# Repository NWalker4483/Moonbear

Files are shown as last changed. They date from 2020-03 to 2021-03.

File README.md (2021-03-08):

<div align="center">

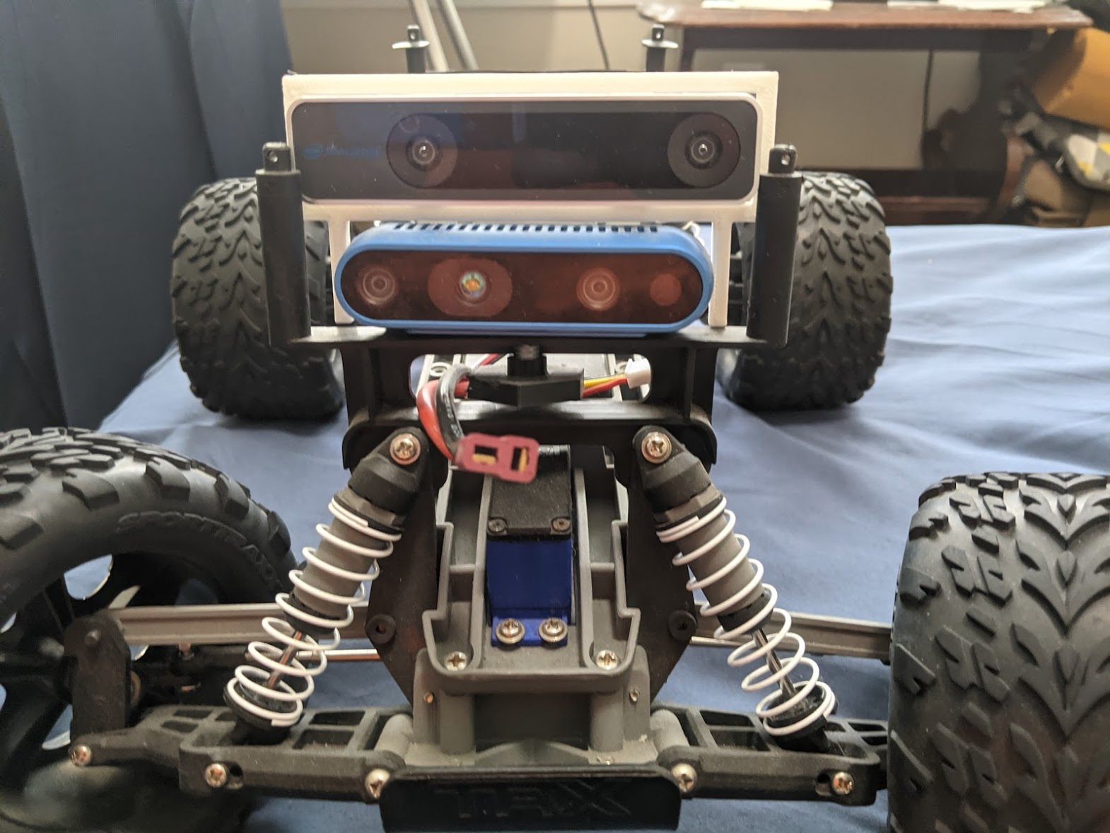
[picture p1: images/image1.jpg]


# Morgan State University’s School of Engineering
## MSU RACECAR V1





# Table of contents
</div>

1. [Introduction](#intro)
2. [The Build Construction](#paragraph1)
   1. Bill of Materials
   2. Compute Modules
   3. Camera(s)
   4. Wi-Fi
   5. Assembly Hardware
3. Hardware Setup
   1. 3D Printed Parts
   2. Wiring
4. The Software Setup
   1. ROS
   2. Arduino
   3. Bluetooth
5. Startup
   1. Manual
   2. Autonomous

## Introduction 
Morgan State University is attempting to delve into the world of Artificial Intelligence. This project is meant to act as a jumping off point for a future endeavors and build a platform that students can learn from and build upon.



## The Build Construction 

### Bill of Materials 

This section lists the parts needed to build the MSU RACECAR. After you have received the parts and confirmed them, proceed to the hardware setup. Some of the parts are 3D printed. In these cases, the STL files have been made available along with recommended print settings.

```Disclaimer: Most of the URLs are from the OEM. You can probably find it cheaper elsewhere, e.g. Amazon.```

### Computing Modules (?) 
|                        |          |        |                                                                                                                                                                                                                                                                                                                |                                |
| ---------------------- | -------- | ------ | -------------------------------------------------------------------------------------------------------------------------------------------------------------------------------------------------------------------------------------------------------------------------------------------------------------- | ------------------------------ |
| Part                   | Quantity | Cost   | URL                                                                                                                                                                                                                                                                                                            | Note                           |
| Jetson Nano            | 1        | $99.00 | https://www.nvidia.com/en-us/autonomous-machines/jetson-store/#jetson-Nano                                                                                                                                                                                                                                     | The 2GB version is also        |
| Arduino Micro          | 1        | $32.00 | https://store.arduino.cc/usa/arduino-micro                                                                                                                                                                                                                                                                     | Generic Version will work also |
### Camera(s) 
|            |          |         |                                                                                                                                                                                                                                                                                                                                                                                                           |      |
| ---------- | -------- | ------- | --------------------------------------------------------------------------------------------------------------------------------------------------------------------------------------------------------------------------------------------------------------------------------------------------------------------------------------------------------------------------------------------------------- | ---- |
| Part       | Quantity | Cost    | URL                                                                                                                                                                                                                                                                                                                                                                                                       | Note |
| INTEL D435 | 1        | $179.00 | https://store.intelrealsense.com/buy-intel-realsense-depth-camera-d435.html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    |      |
| INTEL T265 | 1        | $199.00 | https://store.intelrealsense.com/buy-intel-realsense-tracking-camera-t265.html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 |      |

### Wi-Fi 
|           |          |        |                                                                                                                                                                                                                                                                                                                                                                                                                                                                                              |      |
| --------- | -------- | ------ | -------------------------------------------------------------------------------------------------------------------------------------------------------------------------------------------------------------------------------------------------------------------------------------------------------------------------------------------------------------------------------------------------------------------------------------------------------------------------------------------- | ---- |
| Part      | Quantity | Cost   | URL                                                                                                                                                                                                                                                                                                                                                                                                                                                                                          | Note |
| TL-WN722N | 1        | $16.99 | https://www.tp-link.com/us/home-networking/usb-adapter/tl-wn722n/                                                                                                                                                                                                                                                                                                                                                                                                                            |      |
| USB Hub   | 1        | $12.99 | https://www.amazon.com/Anker-Extended-MacBook-Surface-Notebook/dp/B07L32B9C2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 |      |
### Assembly Hardware + Misc 
|                                              |          |       |                                                                               |                                                                                    |
| -------------------------------------------- | -------- | ----- | ----------------------------------------------------------------------------- | ---------------------------------------------------------------------------------- |
| Part                                         | Quantity | Cost  | URL                                                                           | Note                                                                               |
| Chassis                                      | 1        | $275  |                                                                               | Purchasing a different chassis may make some of the 3-D printed parts unusable     |
| M3 x 6 Machine Screws                        | 4        |       |                                                                               |                                                                                    |
| M5 x 6 Machine Screws                        | 1        |       |                                                                               |                                                                                    |
| 20 x 40 Perfboard                            | 1        | $3    |                                                                               |                                                                                    |
| LM2596 DC-DC Buck Converter Step Down Module | 1        | 14.95 | https://www.amazon.com/LM2596-Converter-Module-Supply-1-23V-30V/dp/B008BHBEE0 | The actual individual part is much cheaper but is often sold only in packs of 5-10 |

## Hardware Setup

### 3D Printed Parts

```All Parts where 3D printed on an Ender 3```
|                                                                                             |                                                                                                                                                                                |                 |              |            |
| ------------------------------------------------------------------------------------------- | ------------------------------------------------------------------------------------------------------------------------------------------------------------------------------ | --------------- | ------------ | ---------- |
| Image(s)                                                                                    | Purpose                                                                                                                                                                        | Supports Needed | Layer Height | Printspeed |
| <img width="200px"  src="images/image3.jpg"/><img width="200px"  src="images/image11.jpg"/> | Acts as a mount for the 2 3D Sensing Cameras. This piece is screwed directly into the front frame of the car as shown in pictures                                              | No              | .28mm        | 150mm/s    |
| <img width="200px"  src="images/image8.jpg"/>                                               | Screws into the rear underside of the Jetson Nano, while the front side rests on a piece of foam on top of the ESC                                                             | Yes             | .28mm        | 150mm/s    |
| <img width="200px"  src="images/image9.jpg"/><img width="200px"  src="images/image10.jpg"/> | Screws into the body of the ESC and attaches to the sides of the arduinos perf board. These pieces are designed specifically for this frame and should slide in place as shown | Yes             | .28mm        | 150mm/s    |
| <img width="200px"  src="images/image12.jpeg"/>                                             | *Take better photo* Acts to extend the head of a 5mm bolt <br>```Before installing drill an approximately 6 mm hole in the middle of the front facing crossbar and shown in the introductory photo```                                                             | No              | .28mm        | 150mm/s    |

### Construction 
#### Power

<img width="200px"  src="images/image14.jpg" alt="Wiring Diagram"/>

In order to power the Jetson Nano we pull power from the RC battery into a Buck Convertor (LM2596) as shown above.
This drops the batteries 7V to a useable 5V. In order to use this with the Jetson Nano, first solder the positive and negative leads of a cut micro USB cable to the output of the LM2596.

   ``` For reference these are the two outer most pins you can check which is positive by connecting both to a multimeter and seeing when the voltage reading is positive ``` 

   Then solder a male header pin in each of the input holes of the device. 

   ```If spare header pins are not available, These can be soldered directly to the board but I find it very convenient to be able to move dangling parts as the design changes.```

   In order to actually connect the convertor to power you'll need to tap into wire somewhere. And our particular case we have an adapter that connects the dean connecter of the battery to the XLC connector for the ESC. By thinly soldering two cables to the output of that adapter it remains usable but also allows us to connect to the header pins we connected earlier.

```A small dab of hot glue at the end of the head can stop the wires from moving around. There's no need to add as much as I did, it makes it harder to plug in```

<img width="200px"  src="images/adapter1.jpg" alt="Wiring Diagram"/>
<img width="200px"  src="images/adapter2.jpg" alt="Wiring Diagram"/>

   Once the leads are soldered and connected to the Voltage convertor. Disconnect the micro usb cable from the Nano and connect the deans connector to the battery. Using a multimeter probe the output pins of the device while turning the blue potentiometer until the output voltage is 5.3 V. Once that's done connect to the Nano and confirm that it boots.

   ```If at this point you plug it in and it doesn't turn on check that the black jumper above the other power connector has been removed. Also the Nano does have built in overvoltage protection so if the input voltage is slightly too high it simply won't turn on```

### Arduino

For the step you're going to need a piece of 20 x 40 Proto board. Solder two female header pin strips on the board lengthwise such that the arduino can slide into them.

```Add Header Photo```

<img width="200px"  src="images/arduino1.jpg" alt="Wiring Diagram"/>

```In earlier version of this had two boards used here which is why you see the extra female that are connected above the blue wire. Ignore it here```

Both the ESC and steering are treated as servos so we'll need to wire male connectors to the Arduino in order to control them.

Connect two of the wires to power. and two of the wires to ground. Connect one wire to pin 9 of the adruino for steering. Connect the second wire to pin 12 of the adruino for the esc. 

```I highly recommend keeping these in groups of 3 with tape or something, just to remember which ones are which because it's impossible to see when the board is slid into place```

<img width="200px"  src="images/slide1.jpg" alt="Wiring Diagram"/>
Take the 2 L shaped pieces you 3D printed earlier And place them into the groves next to the battery as shown above. The pieces will only slide in smoothly when in their correct position

## Software Setup

### General

* Install Ubuntu on the Jetson Nano. https://developer.nvidia.com/embedded/learn/get-started-jetson-Nano-devkit
* Install general dependancies...

```sudo apt-get install git```

* In order to properly use the real sense cameras you'll need to install the drivers for them seperately. Luckily this process has ben mostly automated by the JetsonHacksNano Repo.

### ROS

* Installing ROS melodic with one of the methods below.

#### Method 1

* Follow the instructions to install ROS Melodic Desktop. http://wiki.ros.org/melodic/Installation/Ubuntu

#### Method 2

* Install from the JetsonHacksNano repo. https://github.com/JetsonHacksNano/installROS

```Only the base version is necessary but if you would like to use the GUI tools like rviz in my experience they will run fine.```

Once ROS is installed. Install these ROS package dependencies

``` sudo apt-get install \
ros-melodic-realsense2-camera \
ros-melodic-joy \
ros-melodic-joy-teleop-twist \
ros-melodic-rosserial-arduino \
ros-melodic-rosserial \
ros-melodic-slam-gmapping \
ros-melodic-amcl \
ros-melodic-move-base \
ros-melodic-teb-local-planner \
ros-melodic-robot-upstart \
ros-melodic-pointcloud-to-laserscan
```

```Librealsense is necessary for using the **realsense2-camera** package. Some of the documentation says that it is installed by default but that hasn't worked in my case so I recommend you follow this [tutorial](https://github.com/IntelRealSense/librealsense) to install it separately.```

After the dependencies have been installed clone this repository into your ```workspace/src``` folder as a package and run ```catkin_make; source /devel/setup.bash```

A tutorial on how to make a ROS workspace can be found [here](http://wiki.ros.org/catkin/Tutorials/create_a_workspace)

### Arduino

* In order to get a recent version of the Arduino IDE you're going to need to install it from their official website
* Go to their page select download and download the file associated with your operating system to install.
* Once installed and running, search for your plugged in Arduino device and upload the src.ino from the Arduino folder of this git repo repository.

### OR

* Connect the ```SteeringControlPin```(Pin 9 by default) to the control line for the steering servo.
* Connect the ```ThrottleControlPin```(Pin 12 by default) to the control line for the blue ESC.

## Startup

For either mode it's necessary to power the computer since there is no on or off switch manually plugging and unplugging the RC battery cable is the best way to go about turning the system on and off.

```Though this didn't raise issues during development you should shut down the Nano separately via SSH first```

### Manual

Turning on the setup without connecting **Bluetooth Mode Jumper** will startup the car in bluetooth mode. Then launch the app and start driving.

### Autonomous

 In a new terminal run ```roslaunch rc.launch``` to run the ROS control. After it succesfully connects to the arduino run ```roslaunch mapping.launch``` on either the host machine to run exploration and mapping of the area. The car will stop running when it runs out of search areas

### Sanity Checks

#### librealsense

* Once librealsense is installed properly you should be able to run the realsense-viewer command in terminal. This will bring up a window that allows you to view the data coming from either camera.
* If you're getting a ```[No Realsense devices found]``` error when the device is plugged in check that the udev rules were installed properly. This can be as simple as unplugging and plugging the camera back in.

#### ROS Nodes

* In order to check that all of the notes are launching properly first look at the output of the Ross launch command for info.
* If that doesn't work running the command ```rqt_graph``` will open up a window showing you which notes are sending data to which subscribers.

<img src="" alt="Node Graph"/>

#### Arduino ```WARN: Remove the wheels or prop up before testing```

In order to check that the Arduino is connected and set up properly connect pin 11 to 5v. This will launch the car and serial control mode. By opening up a serial monitor and connecting to the port you found earlier you should be able to send commands directly to the car through this.

* Sending ```T25``` should set the throttle to 25% of the max throttle. 
* Sending ```S90``` should set the steering wheels to 90 degrees aka straight forward.

#### ESC

In order to drive the ESC needs to be *armed* basically the input throttle should hold at 50% for a few seconds. This is indicated by the blinking green light turning a solid green.

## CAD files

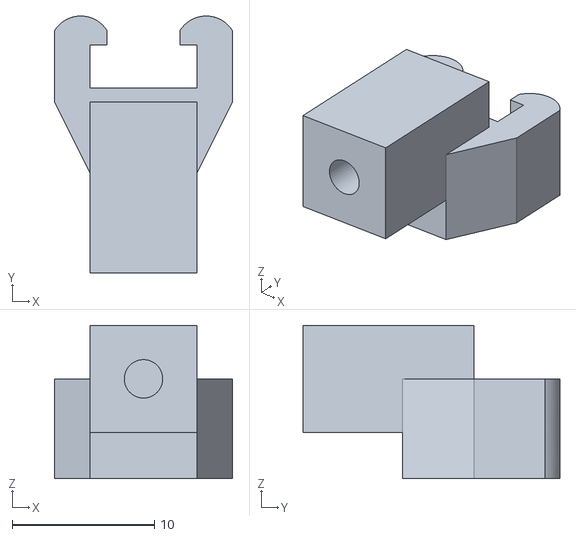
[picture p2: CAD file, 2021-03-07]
stls/Clip.stl
12.5 x 18.0 x 10.8

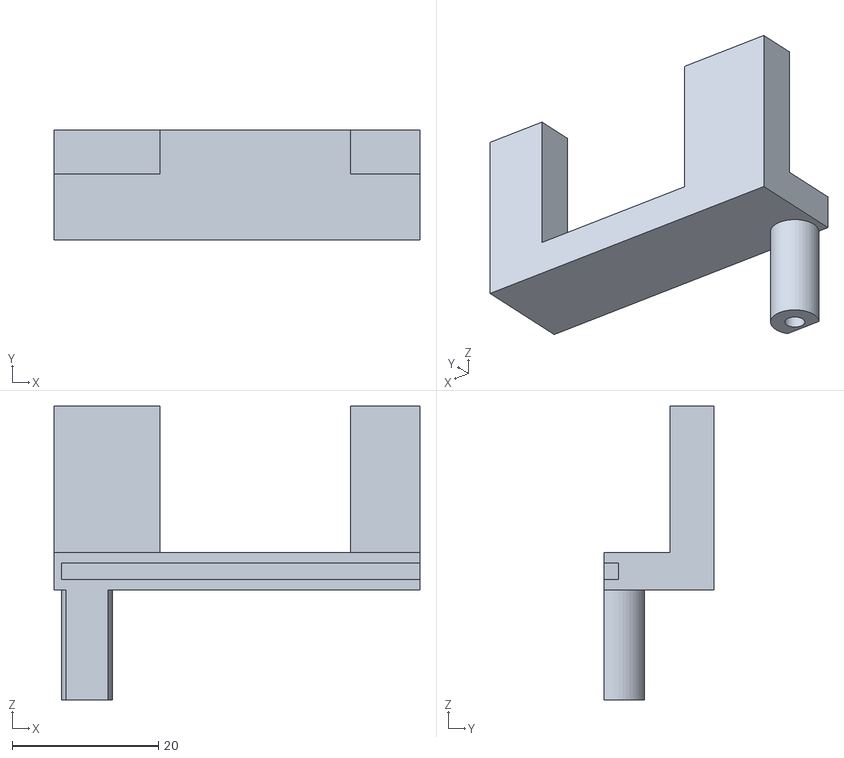
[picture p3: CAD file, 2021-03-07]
stls/Right Wing.stl
50.0 x 15.0 x 40.1

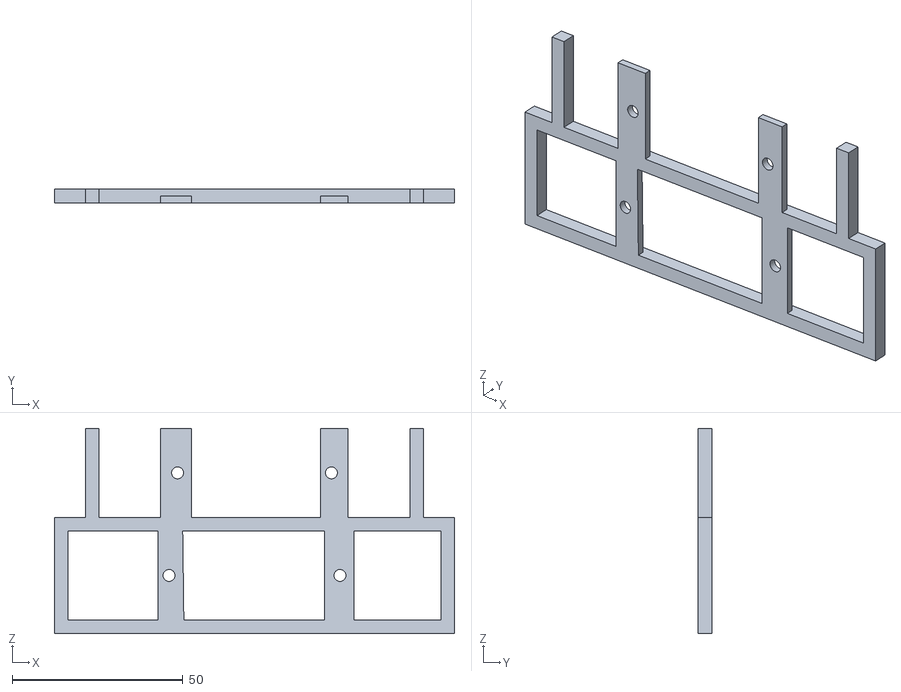
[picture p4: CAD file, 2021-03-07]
stls/Mount.stl
117.0 x 4.00 x 60.0

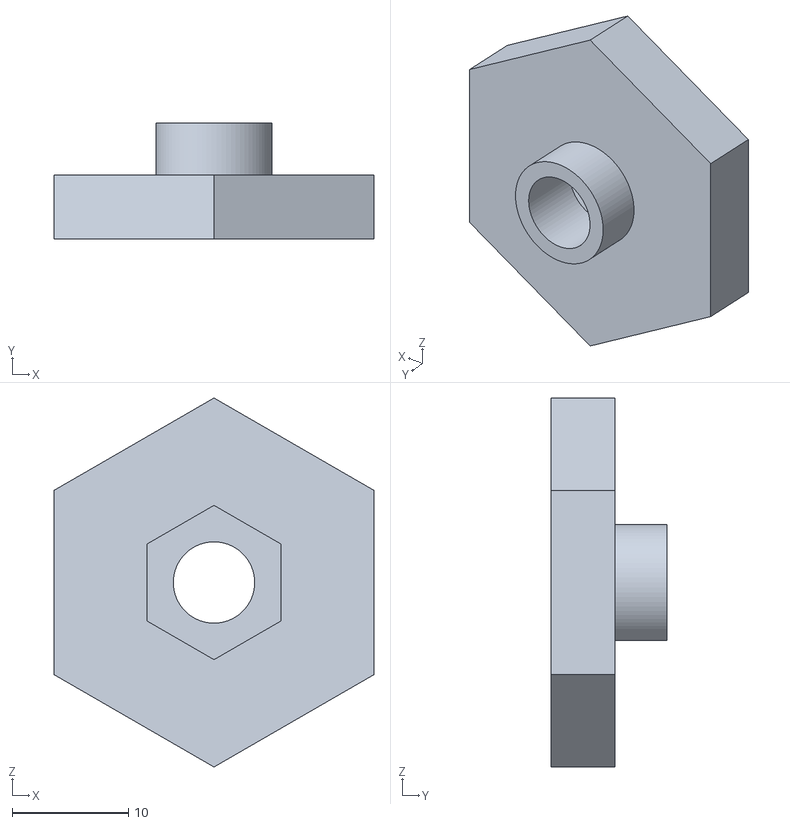
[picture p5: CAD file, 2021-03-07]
stls/Bolt Holder.stl
27.5 x 10.0 x 31.8

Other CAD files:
stls/Left Wing.stl

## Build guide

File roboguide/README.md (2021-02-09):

<div align="center">



# Morgan State University’s School of Engineering
## MSU RACECAR V1





# Table of contents
</div>

1. [Introduction](#intro)
2. [The Build Construction](#paragraph1)
   1. Bill of Materials
   2. Computing Modules (?)
   3. Camera(s)
   4. Wi-Fi
   5. Assembly Hardware
3. Hardware Setup
   1. 3D Printed Parts
   2. Wiring
4. The Software Setup
   1. ROS
   2. Arduino
   3. Bluetooth
5. Startup
   1. Manual
   2. Autonomous

## Introduction 
Morgan State University is attempting to delve into the world of Artificial Intelligence. This project is meant to act as a jumping off point for a future endeavors and build a platform that students can learn from and build upon.



## The Build Construction 

### Bill of Materials 

This section lists the parts needed to build the MSU RACECAR. After you have received the parts and confirmed them, proceed to the hardware setup. Some of the parts are 3D printed. In these cases, the STL files have been made available along with recommended print settings.

```Disclaimer: Most of the URLs are from the OEM. You can probably find it cheaper elsewhere, e.g. Amazon.```

### Computing Modules (?) 
||||||
|---|---|---|---|---|
|Part | Quantity | Cost | URL | Note |
|Jetson Nano|1|$99.00|https://www.nvidia.com/en-us/autonomous-machines/jetson-store/#jetson-nano|The 2GB version is also |
|Arduino Micro|1|$32.00|https://store.arduino.cc/usa/arduino-micro|Generic Version will work also|
|HC-06 Bluetooth Module|1|$11.00|https://www.amazon.com/Wireless-Bluetooth-Receiver-Transceiver-Transmitter/dp/B01MQKX7VP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|Generic Version will work also|

### Camera(s) 
||||||
|---|---|---|---|---|
|Part | Quantity | Cost | URL | Note |
|INTEL D435|1|$179.00|https://store.intelrealsense.com/buy-intel-realsense-depth-camera-d435.html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||
|INTEL T265|1|$199.00|https://store.intelrealsense.com/buy-intel-realsense-tracking-camera-t265.html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||

### Wi-Fi 
||||||
|---|---|---|---|---|
|Part | Quantity | Cost | URL | Note |
|TL-WN722N|1|$16.99|https://www.tp-link.com/us/home-networking/usb-adapter/tl-wn722n/||
|USB Hub|1|$12.99|https://www.amazon.com/Anker-Extended-MacBook-Surface-Notebook/dp/B07L32B9C2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||
### Assembly Hardware + Misc 
||||||
|---|---|---|---|---|
|Part | Quantity | Cost | URL | Note |
|Chassis|1|$275|| Purchasing a different chassis may make some of the 3-D printed parts unusable|
|M3 x 6 Machine Screws|4||||
|M5 x 6 Machine Screws|1||||
|20 x 40 Perfboard|1|$3|||
|LM2596 DC-DC Buck Converter Step Down Module|1|14.95|https://www.amazon.com/LM2596-Converter-Module-Supply-1-23V-30V/dp/B008BHBEE0|The actual individual part is much cheaper but is often sold only in packs of 5-10|
## Hardware Setup
### 3D Printed Parts 
```All Parts where 3D printed on an Ender 3```
||||||
|---|---|---|---|---|
| Image(s) | Purpose | Supports Needed | Layer Height | Printspeed |
|<img width="200px"  src="images/image3.jpg"/><img width="200px"  src="images/image11.jpg"/>|Acts as a mount for the 2 3D Sensing Cameras|No|.28mm| 150mm/s|
|<img width="200px"  src="images/image8.jpg"/>|Screws into the rear underside of the Jetson nano, while the front side rests on a piece of foam on top of the ESC|Yes|.28mm| 150mm/s|
|<img width="200px"  src="images/image9.jpg"/><img width="200px"  src="images/image10.jpg"/>|Screws into the body of the ESC and attaches to the sides of the arduinos perf board|Yes|.28mm| 150mm/s|
|<img width="200px"  src="images/image12.jpeg"/>|Acts to extend the head of a Nmm bolt ```A small hole must be drilled in the frame for the bolt to pass through```|No|.28mm| 150mm/s|
### Wiring

<img width="200px"  src="images/image13.jpg" alt="Wiring Diagram"/>

In order to simplify powering the nano I chose to pull power from the RC battery to a LM2596 as shown above. 

<img width="200px"  src="images/image12.jpg" alt="Wiring Diagram"/>

Connect the Arduino micro and the HC-06 as defined above if the references aren't clear in the photos, the pin definitions can be found at the top of the arduino [script](src/roboguide/arduino/src/src.ino)

## Software Setup
### ROS
#### Method 1: 
   Follow the basic instructions to install Ubuntu 16.04. This requires an at least 16 GB SD card so have one on hand before starting. 
   Once that process is complete, finish by installing ROS melodic with the provided instructions.
#### Method 2: 
   Install from the JetsonHacksNano repo. https://github.com/JetsonHacksNano/installROS

``` Only the base version is necessary but if you would like to use the GUI tools like rviz in my experience they will run fine.```

Once ROS is installed. Install these ROS package dependencies
```
sudo apt-get install \ 
ros-melodic-usb-cam \
ros-melodic-joy \
ros-melodic-joy-teleop-twist \
ros-melodic-compressed-image-transport 
ros-melodic-openni-launch \
ros-melodic-rosserial-arduino \ 
ros-melodic-rosserial \
ros-melodic-slam-gmapping 
```

Librealsense is also necessary for using the realsense camera package. Some of the documentation says that it is installed by default but that hasn't worked in my case so I recommend you follow this [tutorial](https://github.com/IntelRealSense/librealsense) to install it separately.
```You can test this installation using the realsense-viewer command```

After the dependencies have been installed and you cloned the gate repository as a package into your workspace as defined [here](http://wiki.ros.org/catkin/Tutorials/create_a_workspace) run the catkin_make command and run ```/devel/setup.bash```
### Arduino
After which you should clone the git repo into the root of your device. Running the ```./setup.sh``` installation script in the GitHub will install additional dependencies for ROS. Run ```ls /dev/tty*``` to find which port your arduino is attached on. cd into [Moonbear/src/roboguide/arduino/](src/roboguide/arduino/) and run ```ino build; ino upload -p ${port}```

### Bluetooth
Just install the Joy Bluetooth Commander from the play store and pair to the HC-06 device within the app by moving the joystick. 

## Startup
For either mode it's necessary to power the computer since there is no on or off switch manually plugging and unplugging the RC battery cable is the best way to go about turning the system on and off.

```Though this didn't raise issues during development you should shut down the nano separately via SSH first```
### Manual 
Turning on the setup without connecting **Bluetooth Mode Jumper** will startup the car in bluetooth mode. Then launch the App and start driving.
### Autonomous 
 In a new terminal run ```roslaunch rc.launch``` to run the ROS control. After it succesfully connects to the arduino run ```roslaunch mapping.launch``` on either the host machine to run exploration and mapping of the area. The car will stop running when it runs out of search areas
## Bugs

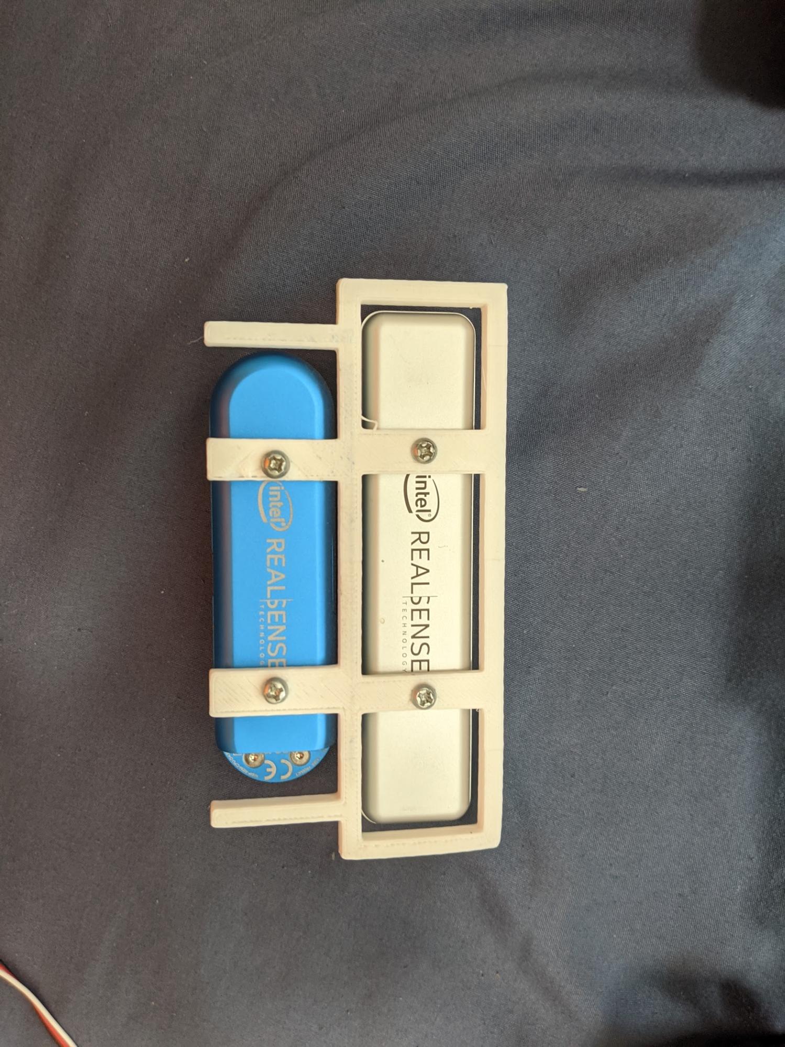
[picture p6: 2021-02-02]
roboguide/images/image3.jpg

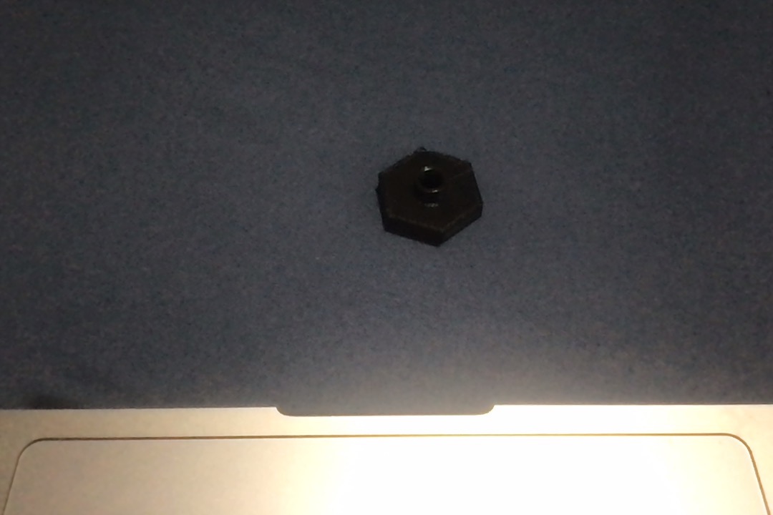
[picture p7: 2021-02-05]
roboguide/images/image12.jpeg

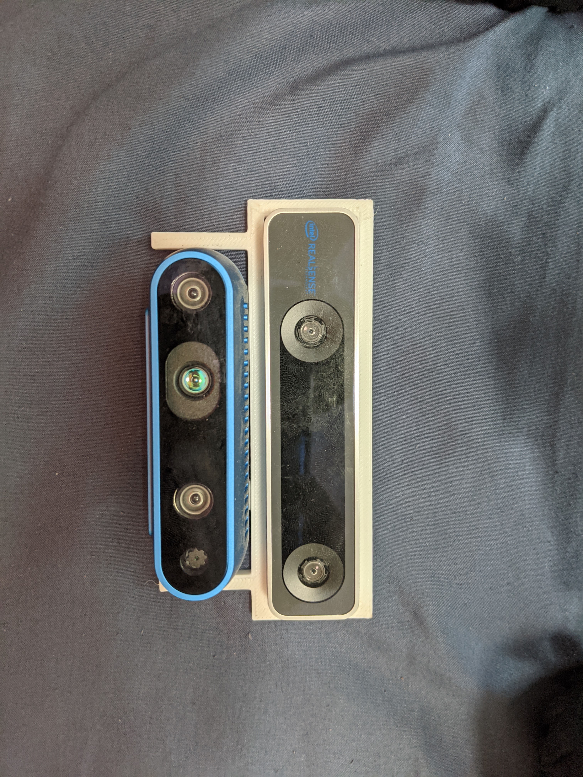
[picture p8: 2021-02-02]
roboguide/images/image11.jpg

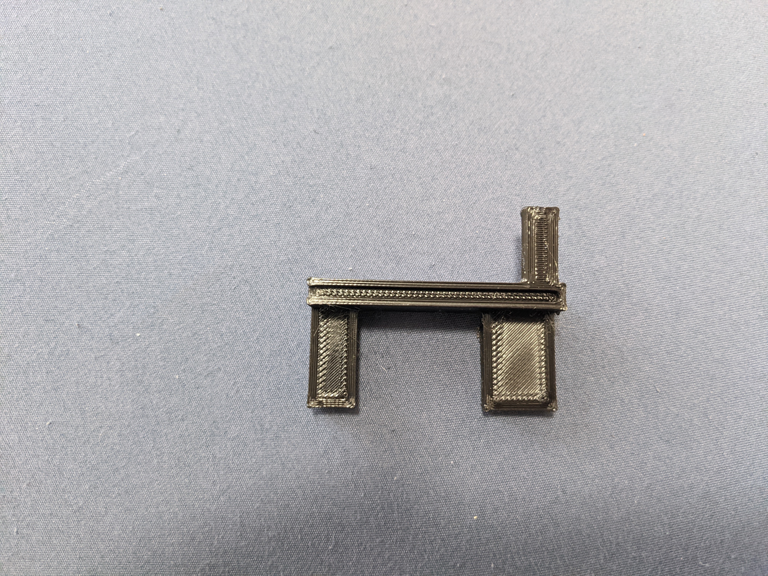
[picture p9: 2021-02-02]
roboguide/images/image9.jpg

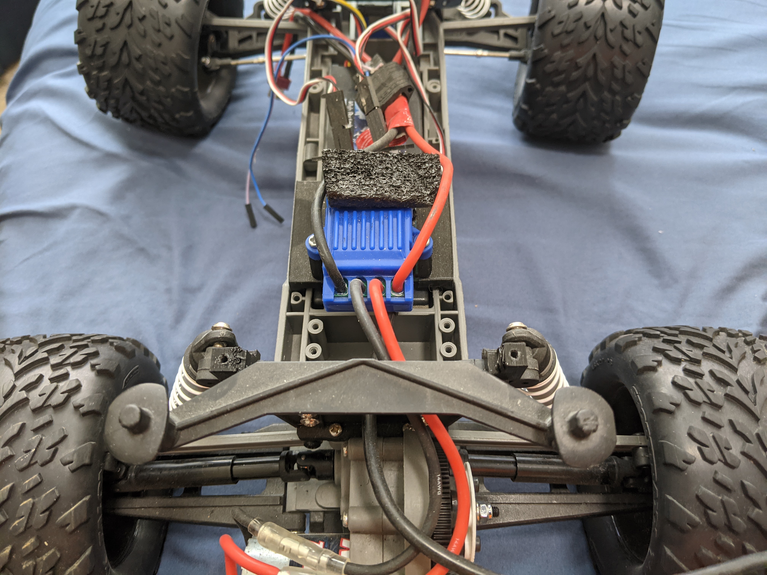
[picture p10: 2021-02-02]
roboguide/images/image10.jpg

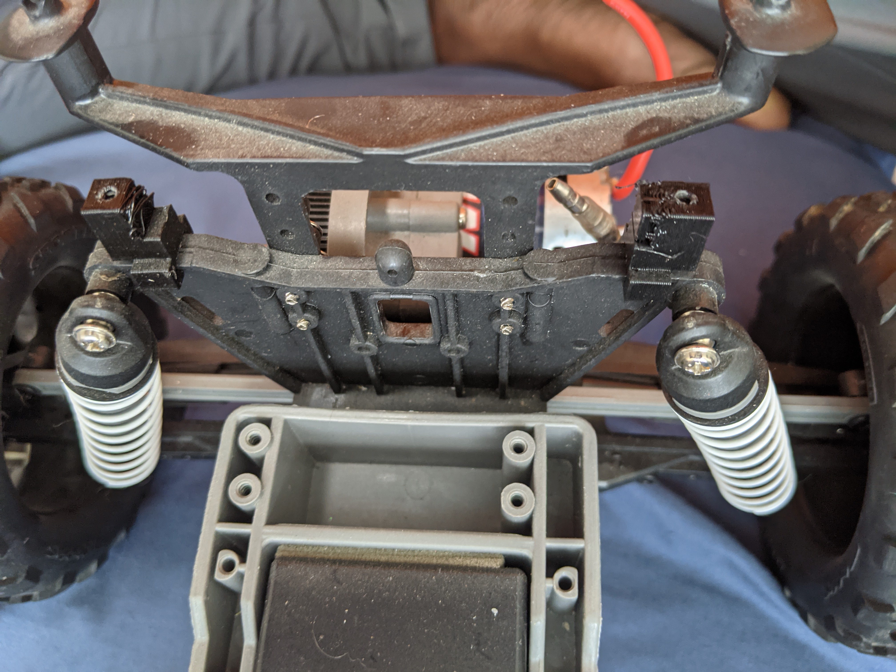
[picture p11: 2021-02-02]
roboguide/images/image8.jpg

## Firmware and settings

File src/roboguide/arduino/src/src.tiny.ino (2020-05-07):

//////////////////////
/* 
  _      _      _
>(.)__ <(.)__ =(.)__
 (___/  (___/  (___/ */
/////////////////////////////
#define StatusModePin 8        // Input Pin acting as the dev jumper
#define BluetoothControlModePin 10    // Input Pin acting as the dev jumper
#define SerialControlModePin 11 // Input Pin acting as the dev jumper
/////////////////////////////////////////////////
#define EncoderPin 2 // Digital Interrupt Pin
/////////////////////////////
#define ThrottleControlPin 12 // Also acts as X when in mixed mode and throttle when in RC Mode
#define SteeringControlPin 9 // Also acts as Y when in mixed mode and steering when in RC Mode
/////////////////////////////
#define CRAWL_SPEED 20     // %
#define MAX_SPEED 36       // %
#define STILL_ALLOWANCE 10 // Loop I
#define REVERSE_ALLOWANCE 10
/////////////////////////////
// Physical Properties of the robot
#define WHEEL_BASE 10        //inches // I forgot Y I did this in inches
#define ENCODER_RESOLUTION 9 // pulses per revolution
#define WHEEL_DIAMETER .12   // m
#define PI 3.1415926535897932384626433832795
/////////////////////////////
//SimpleKalmanFilter simpleKalmanFilter(.25, .25, 0.001);
/////////////////////////////
#define LoopTime 100 // 10 Hz
///////////////
#define    STX          0x02
#define    ETX          0x03   
//////////////

#include <Servo.h>

#include <SoftwareSerial.h>
SoftwareSerial BT_Serial(11,10); // RX | TX

volatile float velocity_estimate = 0;
//float goal_velocity = 0;
//float velocityError = 0;
//float lastVelocityError = 0;
float current_throttle_setting = 0;

ros::NodeHandle nh;

std_msgs::Int16 ticks_msg;
ackermann_msgs::AckermannDriveStamped state_msg;

/////// Bluetooth stuff I aint write this LOL
byte cmd[8] = {0, 0, 0, 0, 0, 0, 0, 0}; // bytes received

double mapf(double val, double in_min, double in_max, double out_min, double out_max)
{
  return (val - in_min) * (out_max - out_min) / (in_max - in_min) + out_min;
}

int parseIntFast(int numberOfDigits)
{
  /*
  This function returns the converted integral number as an int value.
  If no valid conversion could be performed, it returns zero.*/
  char theNumberString[numberOfDigits + 1];
  int theNumber;
  for (int i = 0; i < numberOfDigits; theNumberString[i++] = Serial.read())
  {
    delay(5);
  };
  theNumberString[numberOfDigits] = 0x00;
  theNumber = atoi(theNumberString);
  return theNumber;
}

void getJoystickState(byte data[8])
{
  int joyX = (data[1] - 48) * 100 + (data[2] - 48) * 10 + (data[3] - 48); // obtain the Int from the ASCII representation
  int joyY = (data[4] - 48) * 100 + (data[5] - 48) * 10 + (data[6] - 48);
  joyX = joyX - 200; // Offset to avoid
  joyY = joyY - 200; // transmitting negative numbers

  if (joyX < -100 || joyX > 100 || joyY < -100 || joyY > 100)
    return; // commmunication error

  set_Throttle(joyY);
  set_Steering(map(-joyX, -100, 100, -90, 90));
}

//Globals
unsigned long lastMilli = 0; // time at the end of the last loop
byte mode = 'R';             // ROS Mode
byte ledstatus = LOW;
boolean moving_forward = false;

volatile unsigned long pulses = 0;     // rev counter
volatile unsigned long last_pulse = 0; // time of the last pulse
unsigned long old_pulses = 0;          // pulses since turning on
volatile bool moved = false;

void Blink(int times)
{
  while (times < 0)
  {
    digitalWrite(LED_BUILTIN, HIGH);
    delay(1000);
    digitalWrite(LED_BUILTIN, LOW);
    delay(1000);
    times -= 1;
  }
}

void CheckModeJumpers()
{
  pinMode(StatusModePin, INPUT);
  pinMode(BluetoothControlModePin, INPUT);
  pinMode(SerialControlModePin, INPUT);
  pinMode(LED_BUILTIN, OUTPUT);
  if (digitalRead(StatusModePin) == HIGH)
  {                     // If the dev jumper is connected set dev_mode to true
    Serial.begin(9600); // For Serial Status Info
    Blink(1);
    mode = 'D';
  }
  else if (digitalRead(BluetoothControlModePin) == HIGH)
  {
    BT_Serial.begin(9600); // HC-06 default serial speed is 9600
    Blink(2);
    mode = 'B';
  }
  else if (digitalRead(SerialControlModePin) == HIGH)
  {
    Serial.begin(9600); // HC-06 default serial speed is 9600
    Serial.println("Beginning Simple Serial Mode.");
    Blink(3);
    mode = 'S';
  }
  else
  {
    BT_Serial.begin(9600); // HC-06 default serial speed is 9600
    Blink(2);
    mode = 'B';
  }
}

void getMotorData(unsigned long time)
{
  // double delta_time = double(time) / 1000; // must be in seconds for these formulas
  // rpm = (60*(double(pulses - old_pulses)/ENCODER_RESOLUTION))/delta_time; // 60 is to convert from seconds to minutes
  // old_pulses = pulses
  // state_msg.drive.speed = 1;
}
void EncoderEvent()
{ // Counts pulses on the  Encoder
  if (digitalRead(EncoderPin) == LOW)
  {
    moved = true;
    last_pulse = millis();
  }
}
void set_Steering(int _speed){}
Servo Throttle;
Servo Steering;

void Brake()
{                         // Disengages the brake on the ESC
  moving_forward = false; // Set first to prevent recurion
  Throttle.write(60);
  delay(100);
  Throttle.write(90);
  delay(100);
}

void set_Throttle(int _speed)
{
  if ((_speed < 0) && moving_forward)
  {
    Brake();
  }
  if (_speed > 0)
  {
    moving_forward = true;
  }
  _speed = map(_speed, -100, 100, 55, 145);
  Throttle.write(_speed);
}

void ReadSerialCommands()
{ // Plot PID Values using Serial Plotter
  if (Serial.available())
  {
    char cmdByte = Serial.read();
    int setting;
    switch (cmdByte)
    {
    case 'T': // Change Proportianal Gain
      setting = parseIntFast(4);
      set_Throttle(setting);
      Serial.print("Set Throttle to ");
      Serial.println(current_throttle_setting);
      break;
    case 'S': // Change Integral Gain
      setting = parseIntFast(4);
      set_Steering(setting);
      Serial.print("Set Steering to ");
     // Serial.println(current_steering_angle);
      break;
    }
    Serial.flush();
  }
}

void ReadBluetoothCommands()
{ 
  if (BT_Serial.available() > 0)
  { // data received from smartphone
    delay(2);
    cmd[0] = BT_Serial.read();
    if (cmd[0] == STX)
    {
      int i = 1;
      while (BT_Serial.available() > 0)
      {
        delay(1);
        cmd[i] = BT_Serial.read();
        if (cmd[i] > 127 || i > 7)
          break; // Communication error
        if ((cmd[i] == ETX) && (i == 2 || i == 7))
          break; // Button or Joystick data
        i++;
      }
      //if     (i==2)          getButtonState(cmd[1]);    // 3 Bytes  ex: < STX "C" ETX >
      if (i == 7)
        getJoystickState(cmd); // 6 Bytes  ex: < STX "200" "180" ETX >
    }
  }
}

void setup()
{
  CheckModeJumpers();

  pinMode(SteeringControlPin, OUTPUT);
  pinMode(ThrottleControlPin, OUTPUT);
  pinMode(EncoderPin, INPUT);
  // digitalPinToInterrupt(RightEncoderPinA) == 0
  attachInterrupt(0, EncoderEvent, FALLING); // Trigger right_rpmcounter whenever hall sensor pulses

  Throttle.attach(ThrottleControlPin);
  Steering.attach(SteeringControlPin);

  Throttle.write(90);
  delay(2000);
  Throttle.write(0);
  delay(2000);
  Throttle.write(180);
  delay(2000);
  Throttle.write(90);
  delay(2000);
}

void loop()
{
  unsigned long time = millis(); // time - lastMilli == time passed
  //OUPUTS
  if (time - lastMilli >= LoopTime)
  { // Enter Timed Loop
    getMotorData(time - lastMilli);
    switch (mode)
    {
    case 'D': // Send Status Info
      SendDebugInfo();
      break;
    }
    lastMilli = time;
  }
  //INPUTS
  switch (mode)
  {
  case 'B': // Handle Bluetooth
    ReadBluetoothCommands();
    break;
  case 'A':
    ReadSerialCommands();
    break;
  }
}
//https://answers.ros.org/question/73627/how-to-increase-rosserial-buffer-size/
//http://andrewjkramer.net/motor-encoders-arduino/
//////////////////////
/*
void getMotorData(unsigned long time)
{
  double delta_time = double(time) / 1000;                                     // must be in seconds for these formulas
  rpm = (60 * (double(pulses - oldpulses) / ENCODER_RESOLUTION)) / delta_time; // 60 is to convert from seconds to minutes
  oldpulses = pulses;
  // store your measured speed setting in this variable
  actual_throttle = map(rpm, 0, PERCENT_100_RPM, 0, 100); // 0 :-: 100
  actual_throttle = actual_throttle * (rpm / abs(rpm));   // -100 :-: 100
  //basic velocity inputs
  linear_velocity = (rpm * (WHEEL_DIAMETER / 100.0) * PI) / delta_time; // m/s from rear wheels
  //current_steering_angle;                                               // must be in radians ... I think
  //first get the theta update
  //angular_velocity = linear_velocity * (tan(current_steering_angle) / WHEEL_BASE);
}*/
/*
void PublishTransform()
{
  geometry_msgs::TransformStamped t;

  t.header.frame_id = "/odom";
  t.child_frame_id = "/base_link";
  t.transform.translation.x = current_x;
  t.transform.translation.y = current_y;
  t.transform.translation.z = 0.0;

  t.transform.rotation.x = 0.0;
  t.transform.rotation.y = 0.0;
  t.transform.rotation.z = sin(current_yaw / 2.0);
  t.transform.rotation.w = cos(current_yaw / 2.0);

  t.header.stamp = current_time;

  broadcaster.sendTransform(t);
}*/

void SendDebugInfo()
{ // TODO: Printing all this data causes a large delay in the speed updater
  Serial.print("THROTTLE SETTING: ");
  Serial.println(current_throttle_setting);
  Serial.print("STEERING SETTING: ");
  //Serial.println(current_steering_angle);
  Serial.print("RPM: ");
 // Serial.println(rpm);
  /*
  Serial.print("LINEAR VELOCITY: ");
  Serial.print(linear_velocity);
  Serial.println(" m/s");
  Serial.print("ANGULAR VELOCITY: ");
  Serial.print(angular_velocity);
  Serial.println(" m/s");  
  Serial.print("PULSES SINCE LAST UPDATE: ");
  Serial.println(pulses);*/
  Serial.print("TOTAL PULSES: ");
//  Serial.println(abs(oldpulses));
  Serial.print("\n");
}

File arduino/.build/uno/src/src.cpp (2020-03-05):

#include <Arduino.h>
#include <ros.h>
#include <ros/time.h>
#include <std_msgs/Int16.h>
#include <ackermann_msgs/AckermannDriveStamped.h>
#include <geometry_msgs/Twist.h>
#include <SimpleKalmanFilter.h>
#include <Servo.h>
float CheckClamp(float x);
void UpdatePIDController();
double mapf(double val, double in_min, double in_max, double out_min, double out_max);
void getMotorData(unsigned long time);
void EncoderEvent();
void Brake();
void set_Throttle(int _speed);
void PublishState(unsigned long time);
void setup();
void loop();
#line 1 "src/src.ino"
//////////////////////
/* 
  _      _      _
>(.)__ <(.)__ =(.)__
 (___/  (___/  (___/ */
/////////////////////////////
#define EncoderPin 2 // Digital Interrupt Pin
/////////////////////////////
#define ThrottleControlPin 6 // Also acts as X when in mixed mode and throttle when in RC Mode
#define SteeringControlPin 5 // Also acts as Y when in mixed mode and steering when in RC Mode
/////////////////////////////
#define CRAWL_SPEED 20 // %
#define MAX_SPEED 36   // %
#define STILL_ALLOWANCE 10 // Loop I
#define REVERSE_ALLOWANCE 10
/////////////////////////////
// Physical Properties of the robot
#define WHEEL_BASE 10        //inches // I forgot Y I did this in inches
#define ENCODER_RESOLUTION 9 // pulses per revolution
#define WHEEL_DIAMETER .12    // m
#define PI 3.1415926535897932384626433832795
/////////////////////////////
float P_GAIN = .002;
float I_GAIN = 0.1;
float D_GAIN = 6;
SimpleKalmanFilter simpleKalmanFilter(.25, .25, 0.001);
/////////////////////////////
#define LoopTime 100 // 10 Hz
/////////////////////////////
//#include <ros.h>
//#include <ros/time.h>

//#include <std_msgs/Int16.h>
//#include <ackermann_msgs/AckermannDriveStamped.h>
//#include <geometry_msgs/Twist.h>

//#include <SimpleKalmanFilter.h>
//#include <Servo.h>

bool Clamped = false;
float IntegralTerm = 0;
float DerivativeTerm = 0;
float PID_Output = 0;
volatile float velocity_estimate = 0;
float goal_velocity = 0;
float velocityError = 0;
float lastVelocityError = 0;
float current_throttle_setting = 0;

ros::NodeHandle nh;

std_msgs::Int16 ticks_msg;
ackermann_msgs::AckermannDriveStamped state_msg;

// Bound the input value between x_min and x_max. Also works in anti-windup
float CheckClamp(float x)
{
  float speed = constrain(x, -MAX_SPEED, MAX_SPEED); // Speed Limit
  Clamped = not(speed == x);
  return speed;
}

void UpdatePIDController()
{
  // compute the error between the measurement and the desired value
  velocityError = goal_velocity - velocity_estimate;
  DerivativeTerm = velocityError - lastVelocityError;

  // If the actuator is saturating ignore the integral term
  // if the system is clamped and the sign of the integrator term and the sign of the PID output are the same
  if (Clamped and ((PID_Output / abs(PID_Output)) == (IntegralTerm / abs(IntegralTerm))))
  {
    IntegralTerm += 0;
  }
  else
  {
    IntegralTerm += velocityError;
  }
  // compute the control effort by multiplying the error by Kp
  PID_Output = (velocityError * P_GAIN) + (IntegralTerm * I_GAIN) + (DerivativeTerm * D_GAIN);
  current_throttle_setting = PID_Output;
  state_msg.drive.acceleration = PID_Output;
  // make sure the output value is bounded to 0 to 100 using the bound function defined below
  current_throttle_setting = CheckClamp(current_throttle_setting);
  set_Throttle(current_throttle_setting); // then write it to the LED pin to change control voltage to LED
}

double mapf(double val, double in_min, double in_max, double out_min, double out_max)
{
  return (val - in_min) * (out_max - out_min) / (in_max - in_min) + out_min;
}

//Globals
unsigned long lastMilli = 0; // time at the end of the last loop
byte mode = 'R';             // ROS Mode
byte ledstatus = LOW;
boolean moving_forward = false;

int rpm = 0;
volatile unsigned long pulses = 0; // rev counter
volatile unsigned long last_pulse = 0; // time of the last pulse 
unsigned long old_pulses = 0; // pulses since turning on 
volatile bool moved = false;


ros::Publisher pub_state("/rc_state", &state_msg);

void DriverCallback(const ackermann_msgs::AckermannDriveStamped &);
ros::Subscriber<ackermann_msgs::AckermannDriveStamped> drive("ackermann_cmd", &DriverCallback);

void getMotorData(unsigned long time)
{
  // double delta_time = double(time) / 1000; // must be in seconds for these formulas
  // rpm = (60*(double(pulses - old_pulses)/ENCODER_RESOLUTION))/delta_time; // 60 is to convert from seconds to minutes
  // old_pulses = pulses;
  // state_msg.drive.speed = 1;
}
void EncoderEvent()
{ // Counts pulses on the  Encoder
  if (digitalRead(EncoderPin) == LOW)
  {
    if (last_pulse != 0){
      
    velocity_estimate = ((WHEEL_DIAMETER * PI) / ENCODER_RESOLUTION) / (((millis() - last_pulse))/1000.f);
    velocity_estimate *= moving_forward ? 1 : 1;
    simpleKalmanFilter.updateEstimate(velocity_estimate);
  }
    moved = true;
    last_pulse = millis();
  }
}
Servo Throttle;
Servo Steering;
void Brake()
{                         // Disengages the brake on the ESC
  moving_forward = false; // Set first to prevent recurion
  Throttle.write(60);
  delay(100);
  Throttle.write(90);
  delay(100);
}
void set_Throttle(int _speed)
{                                     
  if ((_speed < 0) && moving_forward)
  {
    Brake();
  }
  if (_speed > 0)
  {
    moving_forward = true;
  }
  _speed = map(_speed, -100, 100, 55, 145);
  Throttle.write(_speed);
}
void DriverCallback(const ackermann_msgs::AckermannDriveStamped &cmd_msg)
{
  // Lin -.5:.5  Ang -1.5:1.5
  goal_velocity = cmd_msg.drive.speed * 5;
  state_msg.drive.jerk = goal_velocity;
  //set_Throttle_Goal();
  Steering.write(mapf(cmd_msg.drive.steering_angle, -.5, .5, 0, 180));
  state_msg.drive.steering_angle = cmd_msg.drive.steering_angle;
}
void PublishState(unsigned long time)
{
  state_msg.header.stamp = nh.now();
  state_msg.drive.speed = simpleKalmanFilter.updateEstimate(velocity_estimate);;
  if (moved == false){state_msg.drive.speed = 0;}
  pub_state.publish(&state_msg);
  moved = false;
}

void setup()
{
  nh.initNode();
  nh.getHardware()->setBaud(57600); // Ros Node uses 57600 by default
  nh.subscribe(drive);
  nh.advertise(pub_state);

  pinMode(ThrottleControlPin, OUTPUT);
  pinMode(EncoderPin, INPUT);
  // digitalPinToInterrupt(RightEncoderPinA) == 0
  attachInterrupt(0, EncoderEvent, FALLING); // Trigger right_rpmcounter whenever hall sensor pulses

  Throttle.attach(ThrottleControlPin);
  Steering.attach(SteeringControlPin);

  Throttle.write(90);
  delay(2000);
  Throttle.write(0);
  delay(2000);
  Throttle.write(180);
  delay(2000);
  Throttle.write(90);
  delay(2000);
  //while(true){}
}

void loop()
{
  nh.spinOnce();
  unsigned long time = millis(); // time - lastMilli == time passed
  if (time - lastMilli >= LoopTime)
  { // Enter Timed Loop
    UpdatePIDController();
    PublishState(time - lastMilli); // Publish and Restart Loop
    lastMilli = time;
  }
}
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

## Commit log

2020-02-26 Added More Arduino Code
2020-02-26 Added Camera Rotat
2020-02-27 Added Code for one way motor driver
2020-02-27 Removed ODOM from arduino
2020-02-28 Added Timer One
2020-02-28 Set pins to match arduino nano
2020-02-28 Added Set Throttle Function for RC Car
2020-02-28 RC CAR ESC + STEERING are controlled
2020-02-28 Improved the software brake on the esc still unreliable
2020-02-28 Arduino Brake still needs work
2020-03-03 Adding PID and ackermann_state P1
2020-03-04 Added Untested PID Control to arduino
2020-05-07 Removed PID Control and added Bluetooth Untested
2020-05-07 Removed ROS for use on micro arduino
2020-05-11 Removed ROS from arduino car to simplify use
2021-02-19 built driver
2021-02-19 cleaned arduino
2021-02-19 Added PID Driver
2021-02-19 var name bug fix
    [driver.py]
2021-02-19 New Driver Code
2021-02-20 Fixed Arduino Ser
2021-03-07 Added STL Files
    [Bolt Holder.stl, Clip.stl, Left Wing.stl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]
